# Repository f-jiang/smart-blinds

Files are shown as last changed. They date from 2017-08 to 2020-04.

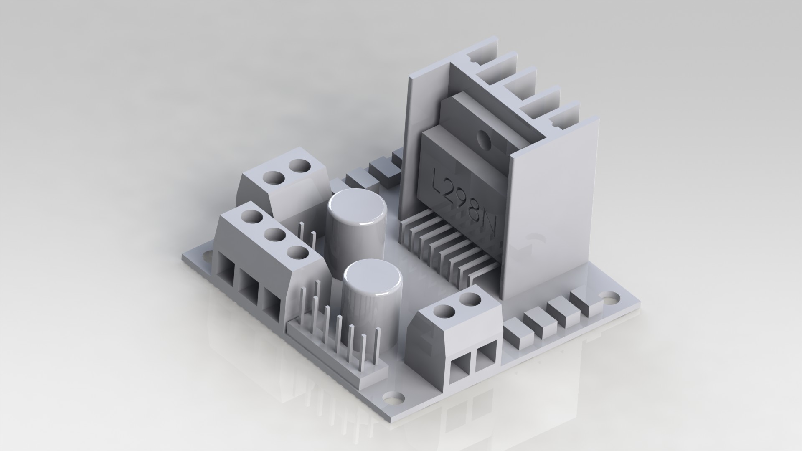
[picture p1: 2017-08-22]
cad/parts/arduino-l298n-1.snapshot.1/FOTO.JPG

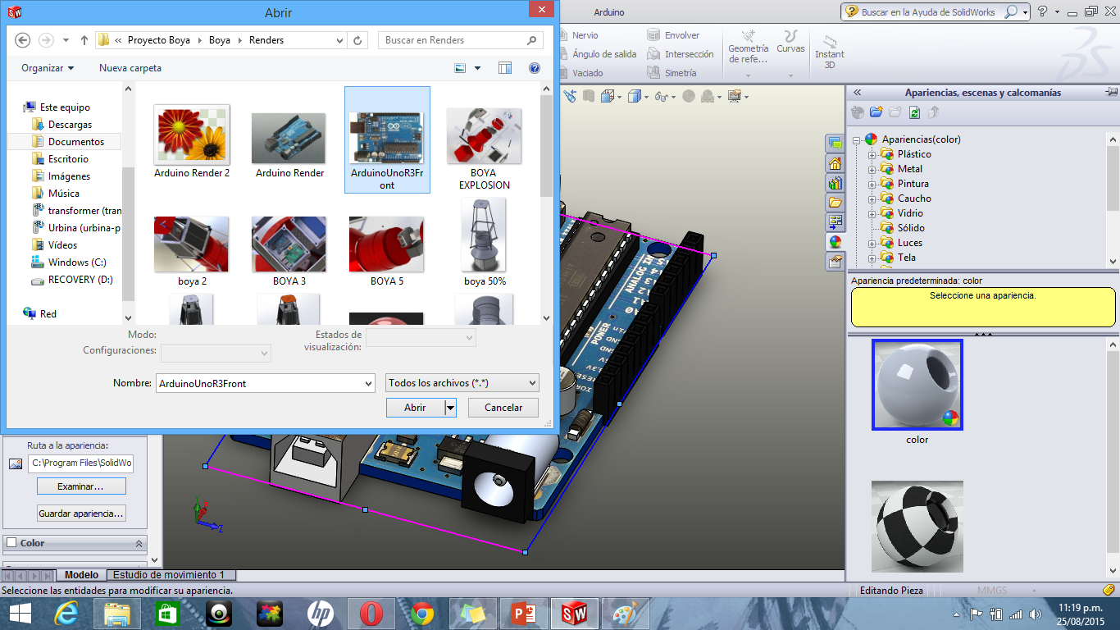
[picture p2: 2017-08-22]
cad/parts/arduino-uno-4.snapshot.3/Renderings/Add Backgroud 2.png

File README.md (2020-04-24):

# smart-blinds
Smart-home blinds attachment with remote-control and scheduling capabilities. Device consists of a stepper motor with an attachment for turning blinds cords and is controlled by an Arduino Uno board. An ESP8266 enables the device to communicate on the network using MQTT. Home Assistant is used for scheduling and remote-control capabilities. The blinds can also be controlled manually using two buttons.

# Repo Contents

## `arduino-src`

Source code for the blinds attachment

```
arduino-src/
├── mqtt_client  # code for ESP8266, used to grant the Arduino board network access thru the MQTT protocol
│   └── mqtt_client.ino
└── smart_blinds  # arduino code for physical control of the blinds attachment
    ├── smart_blinds.h
    ├── smart_blinds.ino  # arduino sketch
    ├── tests.cpp  # "unit tests"
    ├── tests.h
    └── wear_leveled_eeprom_object.h  # utility for storing motor position, etc. in EEPROM in a wear-minimizing way
```

## `cad`

CAD drawings and assemblies. CAD packages used: AutoCAD 2016, SOLIDWORKS 2017

```
cad/
├── exports
│   └── baseplate.DWG  # chassis drawing, to be laser-cut on acrylic
├── parts  # SOLIDWORKS parts
│   ├── arduino-l298n-1.snapshot.1
│   ├── arduino-uno-4.snapshot.3
│   ├── baseplate.SLDPRT  # acrylic chassis
│   ├── cord gear  # 3d-printed blinds cord attachment
│   ├── motherboard-stand-standoff-screw-1.snapshot.1
│   ├── nema-17-nema-23-stepper-motor-mounts-1.snapshot.4
│   ├── nema-17-stepper-motor-13.snapshot.1
│   └── protoboard-5x7-cm.SLDPRT  # perfboard containing mostly power circuitry
└── smart-blinds.SLDASM  # SOLIDWORKS assembly
```

## `docs`

Misc. notes, including technical details, logged work, and unused ideas

## `home-assistant-config`

Setup files for Home Assistant home automation platform

```
home-assistant-config/
├── automations.yaml  # config code to make blinds open/close at sunrise/sunset
├── configuration.yaml  # basic setup including MQTT topic definitions
├── customize.yaml
├── groups.yaml
├── scripts.yaml
└── secrets.yaml
```

# Retrospective
- Could have used ESP32, which has both WiFi capability and enough pins for motor control etc.
- Linear regulators are too hot and inefficient for large voltage stepdowns
- Stepper motors are too big and heavy and lack position control on their own. Could have used a high-torque servo instead.

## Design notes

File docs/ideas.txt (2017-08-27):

mechanical design:
- make the stepper motor's position adjustable
  - attach the motor to a flexible tube-like arm
- reduce blinds cord slippage
  - by using a vertical holder
  - by cutting out a "circle" of holes, allowing the l-bracket to be mounted at a variey of angles

mobile app:
- automatically determine opening and closing times based on location

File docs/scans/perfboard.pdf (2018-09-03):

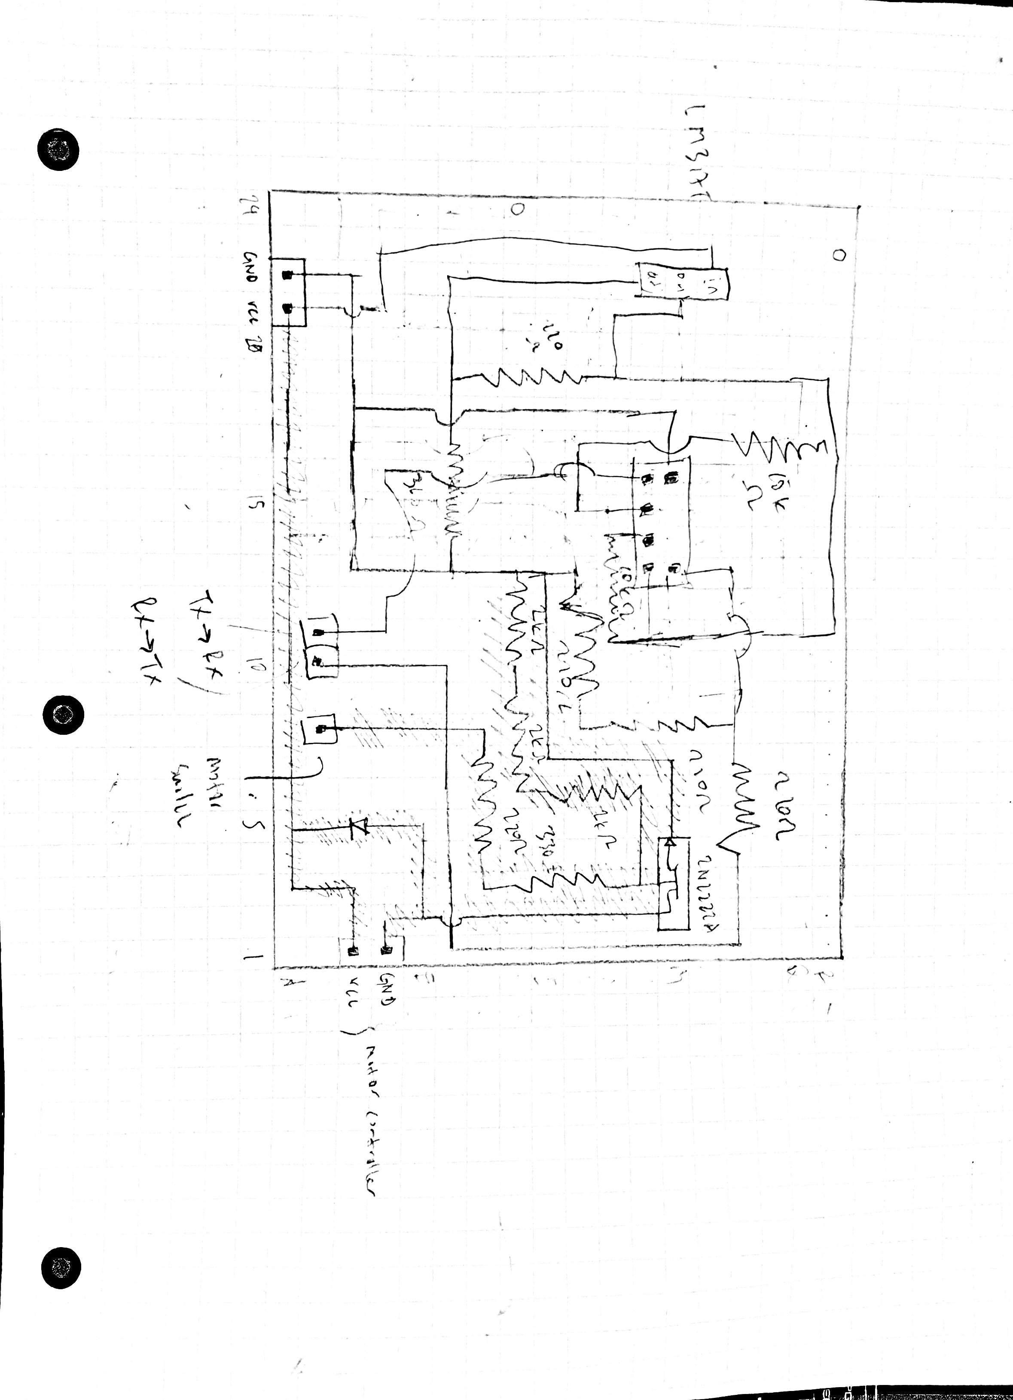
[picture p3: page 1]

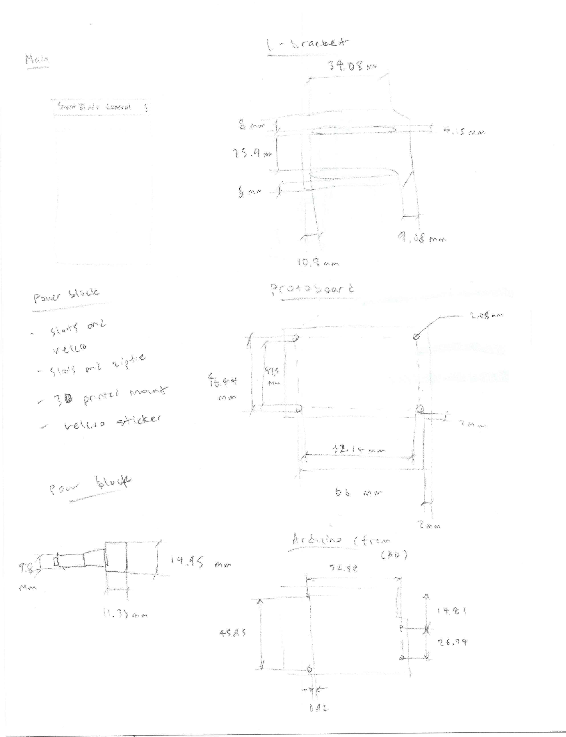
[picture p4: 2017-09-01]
docs/scans/dimensions.jpg

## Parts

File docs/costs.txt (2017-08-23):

- arduino uno: ~$15
- [sensor shield]: $13
- bluetooth module: $10
- motor controller: $14
- motor: $19
- motor bracket: $10
- 12V adapter: $14
- protoboard: $0.30

- acrylic board
- screws, standoffs, etc.
- motor attachments

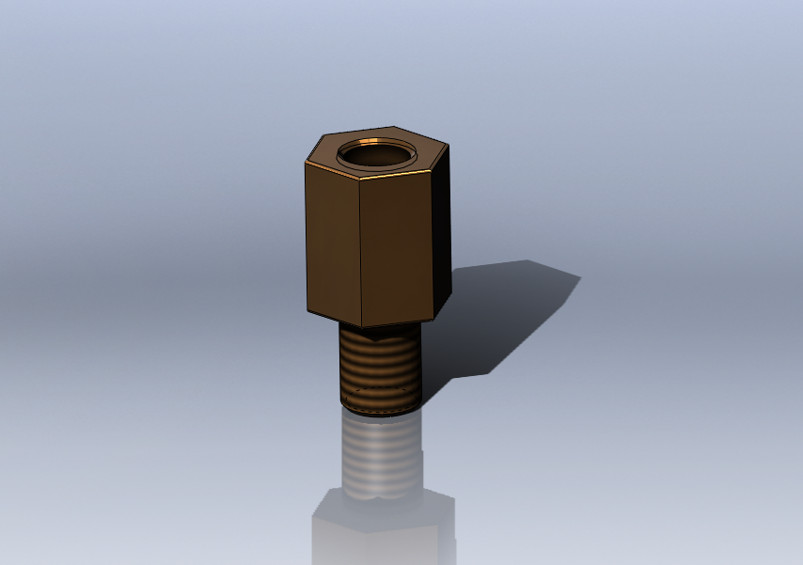
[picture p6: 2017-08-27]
cad/parts/motherboard-stand-standoff-screw-1.snapshot.1/m_standoff.PNG

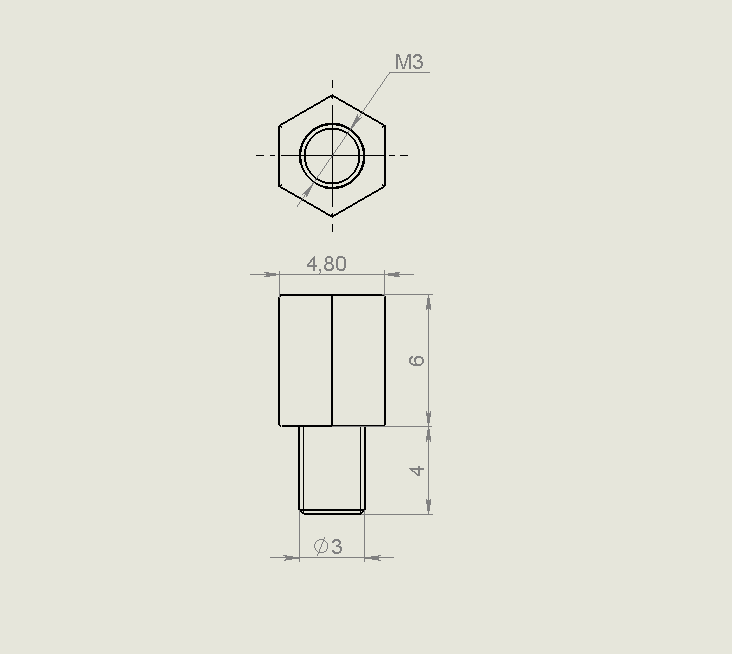
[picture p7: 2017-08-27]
cad/parts/motherboard-stand-standoff-screw-1.snapshot.1/m_standoff_size.PNG

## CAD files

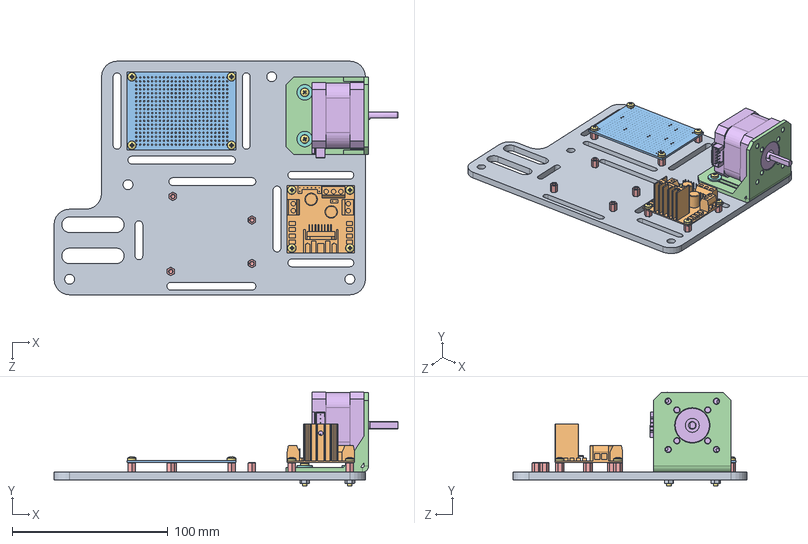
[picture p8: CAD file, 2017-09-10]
cad/smart-blinds.SLDASM
220.9 x 60.0 x 150.0 mm
baseplate
L298N
protoboard-5x7-cm
MotorMount_NEMA
motherboard_stand x 12
Nema 17 motor
pan cross head_am x 12
flat washer regular_am x 4
hex nut style 1_am x 4

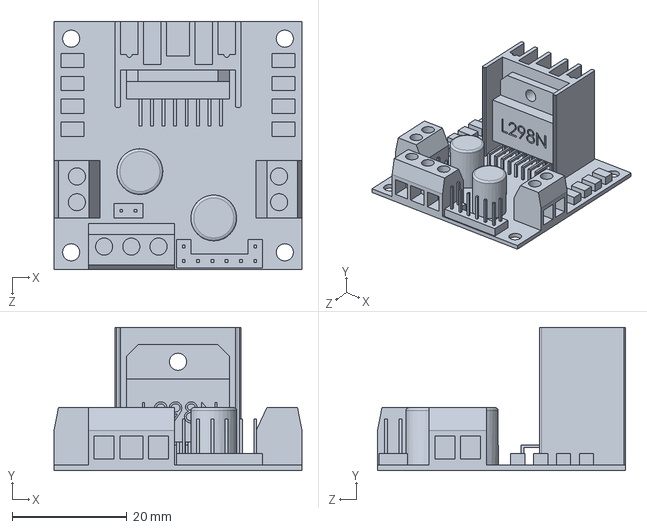
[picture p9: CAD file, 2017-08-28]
cad/parts/arduino-l298n-1.snapshot.1/L298N.SLDPRT
43.3 x 25.0 x 43.3 mm

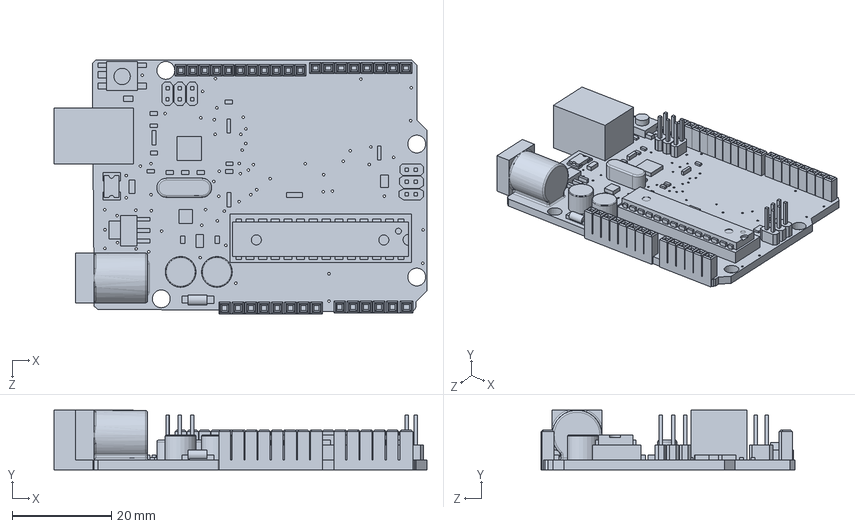
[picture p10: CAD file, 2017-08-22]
cad/parts/arduino-uno-4.snapshot.3/Arduino.SLDPRT
75.0 x 12.0 x 51.0 mm

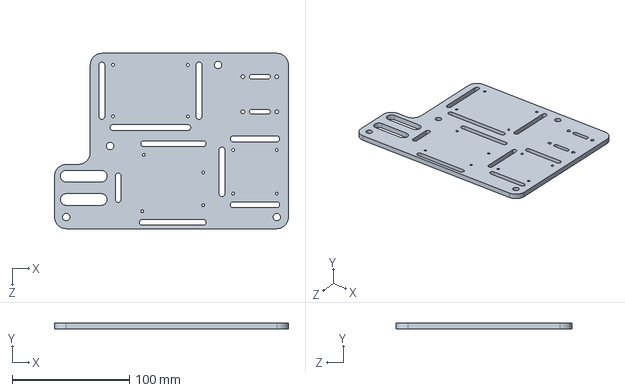
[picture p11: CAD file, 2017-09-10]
cad/parts/baseplate.SLDPRT
200.0 x 5.00 x 150.0 mm

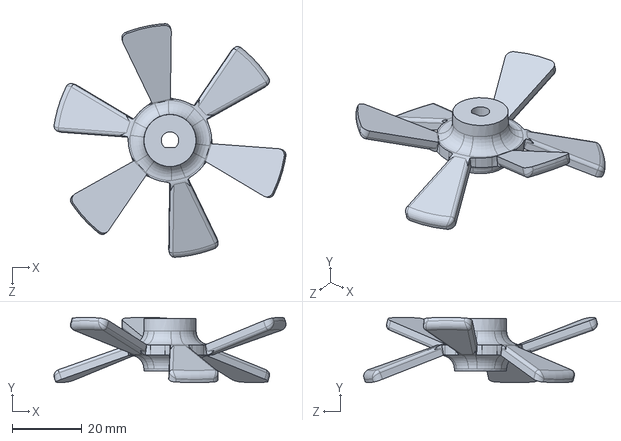
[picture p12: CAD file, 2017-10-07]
cad/parts/cord gear/cord gear.SLDPRT
66.7 x 18.7 x 67.1 mm

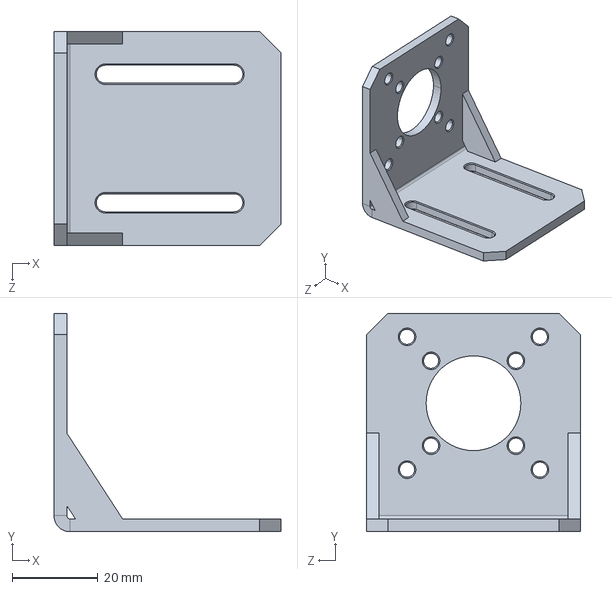
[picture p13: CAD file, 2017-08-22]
cad/parts/nema-17-nema-23-stepper-motor-mounts-1.snapshot.4/NEMA17MotorMount.STEP
53.0 x 51.0 x 50.0 mm

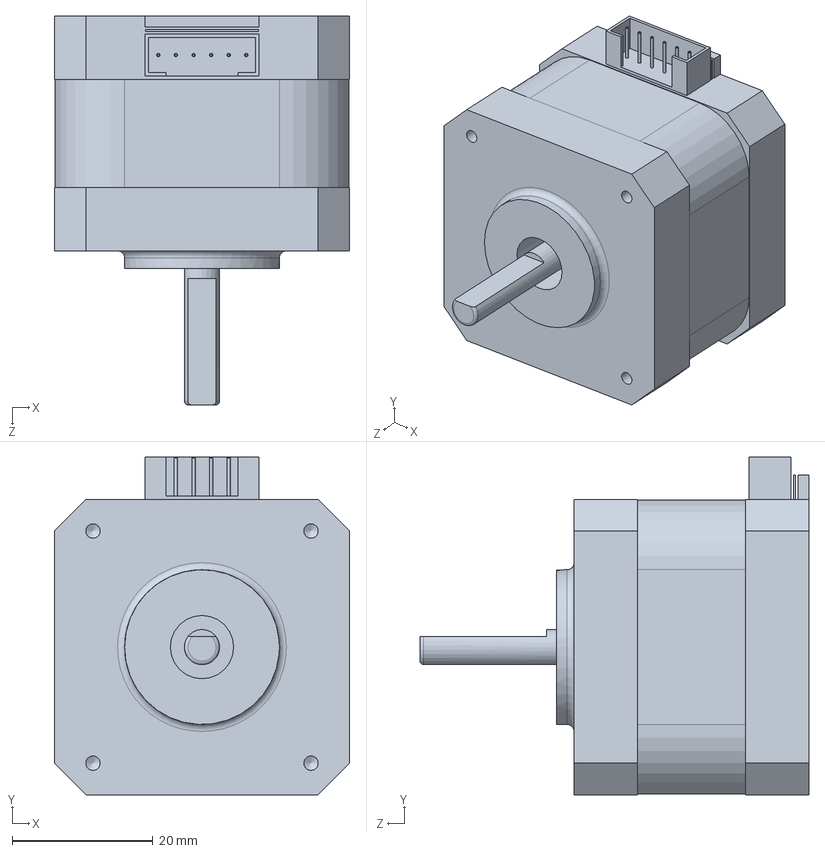
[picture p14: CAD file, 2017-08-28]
cad/parts/nema-17-stepper-motor-13.snapshot.1/Nema 17 motor.SLDPRT
42.0 x 48.0 x 55.3 mm

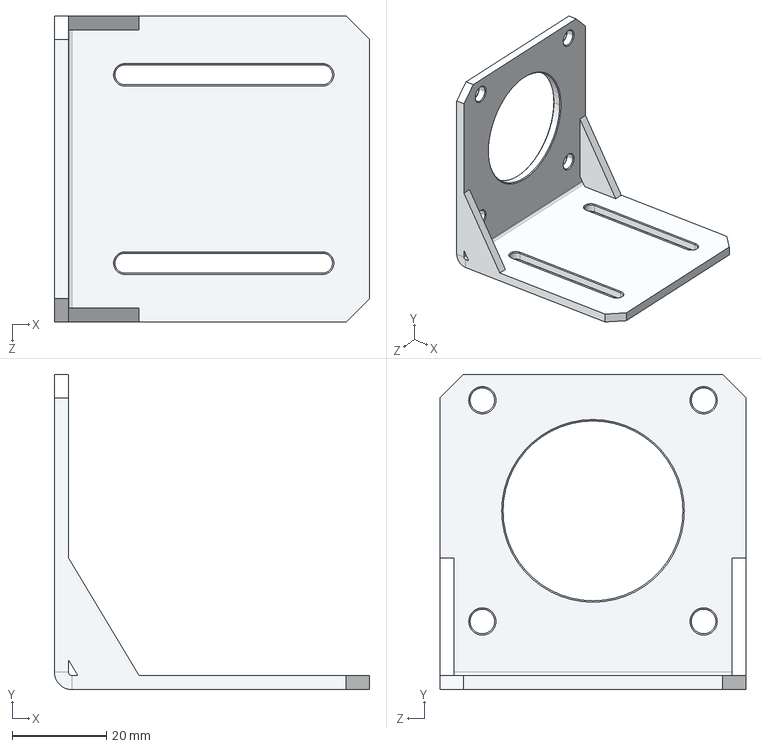
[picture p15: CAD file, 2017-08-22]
cad/parts/nema-17-nema-23-stepper-motor-mounts-1.snapshot.4/NEMA23MotorMount.STEP
67.0 x 67.0 x 65.0 mm

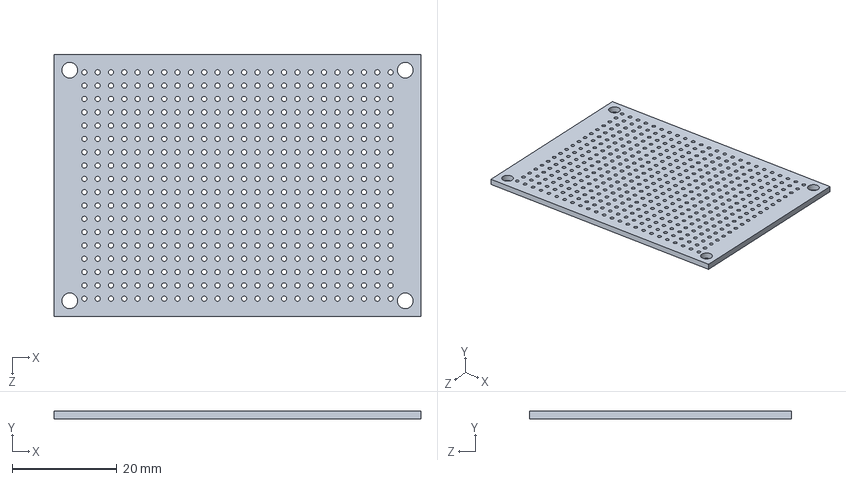
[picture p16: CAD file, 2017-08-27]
cad/parts/protoboard-5x7-cm.SLDPRT
70.0 x 1.50 x 50.0 mm

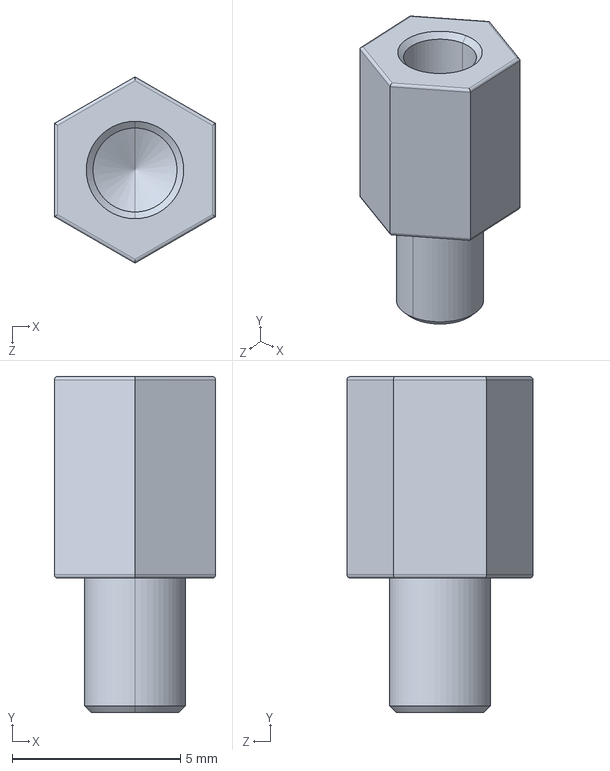
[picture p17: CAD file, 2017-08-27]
cad/parts/motherboard-stand-standoff-screw-1.snapshot.1/motherboard_stand.STP
4.80 x 10.0 x 5.54 mm

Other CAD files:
cad/parts/nema-17-nema-23-stepper-motor-mounts-1.snapshot.4/MotorMount_NEMA.SLDPRT
cad/exports/baseplate.DWG
cad/parts/cord gear/cord gear.STL
cad/parts/motherboard-stand-standoff-screw-1.snapshot.1/motherboard_stand.SLDPRT
cad/parts/nema-17-nema-23-stepper-motor-mounts-1.snapshot.4/NEMA17MotorMount.STL
cad/parts/nema-17-nema-23-stepper-motor-mounts-1.snapshot.4/NEMA23MotorMount.STL

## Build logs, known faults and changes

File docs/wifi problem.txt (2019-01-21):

- tried setting up esp8266 according to several tutorials; each one gave me the same result, which is no response from esp8266
  - http://www.teomaragakis.com/hardware/electronics/how-to-connect-an-esp8266-to-an-arduino-uno/
  - https://www.deviceplus.com/how-tos/arduino-guide/esp8266-setup-tutorial-using-arduino/
 
- also tried talking to esp8266 directly via serial (uploaded blank sketch to arduino): get some junk data but no response of any sort

- tried flashing firmware according to following tutorial:
  - https://www.electronicshub.org/update-flash-esp8266-firmware/
    - result: status FAIL or ERROR; also the DETECTED INFO section is blank and before failure the status is stuck at SYNC, even though serial port is detected
    
1/13/19:
  - plugged new esp into perboard circuit; used 115200 baud, and was getting response from esp but garbled
    - also the blue led was staying on for longer and longer each time
  - then built deviceplus circuit on breadboard, got clear responses from esp at 9600 baud
  - put same esp back into perfboard circuit but now using 9600 baud; now esp blue led always on and no longer getting responses
    - this is how the second esp broke
    - when reset esp will still output firmware info, same as second "broken" esp
- ideas for what happened
  - there is something wrong with my perfboard circuit: either incorrect schematics (didn't follow device plus circuit accurately) or poor layout of components, resulting in esp getting damaged
  - the device plus circuit is flawed
  - maybe esp is fixable
  
1/19/19:
- with ftdi converter, boot message at 74880 baud, but no response from AT commands regardless of baud
- another reason not working:
  - maybe board is just bricked not broken -> try reflashing firmware using esptool.py according to this guide: https://bbs.espressif.com/viewtopic.php?t=4597#p15844
    - step 1: set up python esptool:
      - erase flash - done
    - step 2: get and flash firmware
    - worked
    - commands to enter for reflashing for 8Mb flash:
      esptool.py erase_flash
      esptool.py --port <port> write_flash -fm qio 0x00000 boot_v1.7.bin
      esptool.py --port <port> write_flash -fm qio 0x01000 user1.1024.new.2.bin
      esptool.py --port <port> write_flash -fm qio 0xfc000 esp_init_data_default.bin
      esptool.py --port <port> write_flash -fm qio 0x7e000 blank.bin
- so true cause: AT+IPR=9600 bricks the board
  - instead use AT+UART_DEF to change the baud rate
  - For example 9600 baudrate / 8 data bits / 1 stop bits and none parity and flow control
    AT+UART_DEF=9600,8,1,0,0

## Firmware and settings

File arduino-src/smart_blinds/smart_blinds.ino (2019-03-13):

/* #define TEST */
#define DEBUG

#include "smart_blinds.h"

#include <stdlib.h>
#include <SoftwareSerial.h>
#ifdef TEST
#include "tests.h"
#endif
#include "wear_leveled_eeprom_object.h"

#define SERIAL_BAUD_RATE            9600
#define SOFTWARE_SERIAL_BAUD_RATE   9600

#define STEPPER_A                   2
#define STEPPER_B                   3
#define STEPPER_C                   4
#define STEPPER_D                   5
#define RPM                         15
#define STEP_ANGLE                  1.8
#define STEPS_PER_REVOLUTION        (360.0 / STEP_ANGLE)

#define RELAY_PIN                   6

#define BUTTON_PIN                  7

#define ESP_RX                      8
#define ESP_TX                      9

#define COMMAND_TILT                't'
#define COMMAND_CALIBRATE_HIGH      'h'
#define COMMAND_CALIBRATE_LOW       'l'

#define STR_BUF_LEN                 10

Stepper stepper(STEPS_PER_REVOLUTION, STEPPER_A, STEPPER_B, STEPPER_C, STEPPER_D);
Relay relay(RELAY_PIN, Relay::Mode::NORMALLY_OPEN);
ace_button::AceButton btn(BUTTON_PIN);
SoftwareSerial esp(ESP_RX, ESP_TX);

size_t circularQueueItemCount = EEPROM_SIZE_BYTES /
                                (3 * WearLeveledEepromObject<stepper_pos_t>::circularQueueItemSize());
WearLeveledEepromObject<stepper_pos_t> stepperPos(0, circularQueueItemCount);
WearLeveledEepromObject<stepper_pos_t> stepperPosLowerLimit(EEPROM_SIZE_BYTES / 3, circularQueueItemCount);
WearLeveledEepromObject<stepper_pos_t> stepperPosUpperLimit(2 * EEPROM_SIZE_BYTES / 3, circularQueueItemCount);
stepper_pos_t eepromValue;

void setup()
{
    Serial.begin(SERIAL_BAUD_RATE);

    if (stepperPos.get(eepromValue) == 0xFFFF &&
        stepperPosLowerLimit.get(eepromValue) == 0xFFFF &&
        stepperPosUpperLimit.get(eepromValue) == 0xFFFF)
    {
#ifdef DEBUG
        Serial.println("no position or limits in storage; using defaults instead");
#endif
        eepromValue = STEPPER_POSITION_DEFAULT;
        stepperPos.put(eepromValue);
        eepromValue = STEPPER_POSITION_LOWER_LIMIT_DEFAULT;
        stepperPosLowerLimit.put(eepromValue);
        eepromValue = STEPPER_POSITION_UPPER_LIMIT_DEFAULT;
        stepperPosUpperLimit.put(eepromValue);
#ifndef DEBUG
    }
#else
    } else {
        stepper_pos_t pos, lower_limit, upper_limit;
        stepperPos.get(pos);
        stepperPosLowerLimit.get(lower_limit);
        stepperPosUpperLimit.get(upper_limit);

        Serial.print("found following in storage: position ");
        Serial.print(pos);
        Serial.print(", lower limit ");
        Serial.print(lower_limit);
        Serial.print(", upper limit ");
        Serial.println(upper_limit);
    }
#endif

    relay.begin();
    stepper.setSpeed(RPM);
#ifdef DEBUG
    Serial.print("stepper speed set to ");
    Serial.print(RPM);
    Serial.println(" rpm");
#endif

    pinMode(BUTTON_PIN, INPUT_PULLUP);
    btn.setEventHandler(handleBtnEvent);

    relay.open();

    esp.begin(SOFTWARE_SERIAL_BAUD_RATE);

#ifdef TEST
    Serial.println("Running tests...");
    test();
    Serial.println("Tests complete and successful");
#endif
}

void loop()
{
#ifndef TEST
    btn.check();

    if (esp.available() > 0) {
        String data;
        while (esp.available() > 0) {
            data += (char) esp.read();
        }

#ifdef DEBUG
        Serial.print("received data from serial: ");
        Serial.println(data);
#endif

        char command = data.charAt(0);
        data.remove(0, 1);
        int value = data.toInt();
        stepper_pos_t new_value;
        char buf[STR_BUF_LEN];

#ifdef DEBUG
        Serial.print("values extracted from incoming serial data: command ");
        Serial.print(command);
        Serial.print(", value ");
        Serial.println(value);
#endif

        switch (command) {
            case COMMAND_TILT:
                if (data.length() > 0) {
                    setStepperPos((stepper_pos_t) value);
                }

                getStepperPos(new_value);
                sprintf(buf, "%c%d", COMMAND_TILT, new_value);
                esp.write(buf);

#ifdef DEBUG
                Serial.print("new stepper position: ");
                Serial.println(new_value);
#endif
                break;
            case COMMAND_CALIBRATE_HIGH:
                if (data.length() > 0) {
                    relay.open();
                    setStepperPosUpperLimit((stepper_pos_t) value);
                }

                getStepperPosUpperLimit(new_value);
                sprintf(buf, "%c%d", COMMAND_CALIBRATE_HIGH, new_value);
                esp.write(buf);

#ifdef DEBUG
                Serial.print("new stepper upper limit: ");
                Serial.println(new_value);
#endif
                break;
            case COMMAND_CALIBRATE_LOW:
                if (data.length() > 0) {
                    relay.open();
                    setStepperPosLowerLimit((stepper_pos_t) value);
                }

                getStepperPosLowerLimit(new_value);
                sprintf(buf, "%c%d", COMMAND_CALIBRATE_LOW, new_value);
                esp.write(buf);

#ifdef DEBUG
                Serial.print("new stepper lower limit: ");
                Serial.println(new_value);
#endif
                break;
            default:
#ifdef DEBUG
                Serial.println("not a valid command");
#endif
                break;
        }
    }

    delay(100);
#endif
}

void handleBtnEvent(ace_button::AceButton* /*button*/, uint8_t eventType, uint8_t /*state*/)
{
    switch (eventType) {
        case ace_button::AceButton::kEventReleased:
        {
#ifdef DEBUG
            Serial.println("button press detected");
#endif

            stepper_pos_t pos, lowerLimit;
            stepperPos.get(pos);
            stepperPos.get(lowerLimit);

            setStepperPos((pos == lowerLimit) ?
                          stepperPosUpperLimit.get(eepromValue) : stepperPosLowerLimit.get(eepromValue));

            stepper_pos_t new_value;
            char buf[STR_BUF_LEN];
            getStepperPos(new_value);
            sprintf(buf, "%d", new_value);
            esp.write(COMMAND_TILT);
            esp.write(buf);

#ifdef DEBUG
            Serial.print("new stepper position: ");
            Serial.print(new_value);
            Serial.print(" (");
            Serial.print((new_value == lowerLimit) ? "lower" : "upper");
            Serial.println(" limit)");
#endif
            break;
        }
        default:
            break;
    }
}

bool isPosInverted()
{
    return stepperPosUpperLimit.get(eepromValue) < stepperPosLowerLimit.get(eepromValue);
}

bool isStepperCalibrated()
{
    return (stepperPos.get(eepromValue) != STEPPER_POSITION_DEFAULT) &&
           (stepperPosLowerLimit.get(eepromValue) != STEPPER_POSITION_LOWER_LIMIT_DEFAULT) &&
           (stepperPosUpperLimit.get(eepromValue) != STEPPER_POSITION_UPPER_LIMIT_DEFAULT);
}

bool isPosOutOfBounds(stepper_pos_t pos)
{
    bool retval;

    bool inverted = isPosInverted();
    if ((!inverted &&
         (stepperPosLowerLimit.get(eepromValue) <= pos) &&
         (pos <= stepperPosUpperLimit.get(eepromValue))) ||
        (inverted &&
         (stepperPosUpperLimit.get(eepromValue) <= pos) &&
         (pos <= stepperPosLowerLimit.get(eepromValue)))) {
        retval = false;
    } else {
        retval = true;
    }

    return retval;
}

bool getStepperPos(stepper_pos_t& pos)
{
    bool success = false;

    if (true) { // TODO temp
        success = true;
        stepperPos.get(pos);
    }

    return success;
}

bool setStepperPos(stepper_pos_t pos)
{
    bool success = false;

    if (!isPosOutOfBounds(pos)) {
        success = true;

        stepper_pos_t stepValue;

        if (isPosInverted()) {
            stepValue = stepperPos.get(eepromValue) - pos;
        } else {
            stepValue = pos - stepperPos.get(eepromValue);
        } /* else {
            success = false;
        } */

        if (success && stepValue != 0) {
            relay.close();
            stepper.step(stepValue);
            relay.open();
            stepperPos.put(pos);
        }
#ifndef DEBUG
    }
#else
        Serial.print("set stepper position to ");
        Serial.println(pos);
    } else if (!relay.isClosed()) {
        Serial.println("setting stepper position failed because relay is open");
    } else {
        Serial.println("setting stepper position failed because new position is out-of-bounds");
    }
#endif

    return success;
}

bool getStepperPosLowerLimit(stepper_pos_t& pos)
{
    bool success = false;

    if (true) { // TODO temp
        success = true;
        stepperPosLowerLimit.get(pos);
    }

    return success;
}

// TODO enforce lower != upper?
bool setStepperPosLowerLimit(stepper_pos_t pos)
{
    bool success = false;

    if (!relay.isClosed()) {
        success = true;
        stepperPosLowerLimit.put(pos);
    }

    return success;
}

bool getStepperPosUpperLimit(stepper_pos_t& pos)
{
    bool success = false;

    if (true) { // TODO temp
        success = true;
        stepperPosUpperLimit.get(pos);
    }

    return success;
}

// TODO enforce lower != upper?
bool setStepperPosUpperLimit(stepper_pos_t pos)
{
    bool success = false;

    if (!relay.isClosed()) {
        success = true;
        stepperPosUpperLimit.put(pos);
    }

    return success;
}

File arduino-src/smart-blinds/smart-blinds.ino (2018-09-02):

#define TEST_DEBUG

#include "smart-blinds.h"

#ifdef TEST_DEBUG
#include "tests.h"
#endif  // TEST_DEBUG

#define STEPPER_A               8
#define STEPPER_B               9
#define STEPPER_C               10
#define STEPPER_D               11
#define RPM                     15
#define STEP_ANGLE              1.8
#define STEPS_PER_REVOLUTION    (360.0 / STEP_ANGLE)

#define RELAY_PIN               6

#define BUTTON_PIN              7

Stepper stepper(STEPS_PER_REVOLUTION, STEPPER_A, STEPPER_B, STEPPER_C, STEPPER_D);
Relay relay(RELAY_PIN, Relay::Mode::NORMALLY_OPEN);
int stepperPos = STEPPER_POSITION_DEFAULT;
int stepperPosLowerLimit = STEPPER_POSITION_LOWER_LIMIT_DEFAULT;
int stepperPosUpperLimit = STEPPER_POSITION_UPPER_LIMIT_DEFAULT;

void setup()
{
    Serial.begin(9600);

    // TODO load position from eeprom

    relay.begin();
    stepper.setSpeed(RPM);

    relay.open();

#ifdef TEST_DEBUG
    Serial.println("Running tests...");
    test();
    Serial.println("Tests complete and successful");
#endif  // TEST_DEBUG
}

void loop()
{
}

StepperPositionScaleType getStepperPositionScaleType()
{
    StepperPositionScaleType retval;

    if (stepperPosLowerLimit <= stepperPosUpperLimit) {
        retval = NORMAL;
    } else {
        retval = INVERTED;
    }

    return retval;
}

bool isStepperCalibrated()
{
    return (stepperPos != STEPPER_POSITION_DEFAULT) &&
           (stepperPosLowerLimit != STEPPER_POSITION_LOWER_LIMIT_DEFAULT) &&
           (stepperPosUpperLimit != STEPPER_POSITION_UPPER_LIMIT_DEFAULT);
}

bool isPosOutOfBounds(int pos)
{
    bool retval;

    StepperPositionScaleType scaleType = getStepperPositionScaleType();
    if (((scaleType == NORMAL) &&
         (stepperPosLowerLimit <= pos) &&
         (pos <= stepperPosUpperLimit)) ||
        ((scaleType == INVERTED) &&
         (stepperPosUpperLimit <= pos) &&
         (pos <= stepperPosLowerLimit))) {
        retval = false;
    } else {
        retval = true;
    }

    return retval;
}

bool getStepperPos(int& pos)
{
    bool success = false;

    if (true) { // TODO temp
        success = true;
        pos = stepperPos;
    }

    return success;
}

bool setStepperPos(int pos)
{
    bool success = false;

    if (relay.isClosed() && !isPosOutOfBounds(pos)) {
        success = true;

        int stepValue;
        StepperPositionScaleType scaleType = getStepperPositionScaleType();

        if (scaleType == NORMAL) {
            stepValue = pos - stepperPos;
        } else if (scaleType == INVERTED) {
            stepValue = stepperPos - pos;
        } else {
            success = false;
        }

        if (success) {
            stepper.step(stepValue);
            stepperPos = pos;
        }
    }

    return success;
}

bool incrementStepperPos()
{
    bool success = true;

    int newPos;
    StepperPositionScaleType scaleType = getStepperPositionScaleType();

    if (scaleType == NORMAL) {
        newPos = stepperPos + STEP_INCREMENT_SIZE;
    } else if (scaleType == INVERTED) {
        newPos = stepperPos - STEP_INCREMENT_SIZE;
    }

    if (success) {
        success = setStepperPos(newPos);
    }

    return success;
}

bool decrementStepperPos()
{
    bool success = true;

    int newPos;
    StepperPositionScaleType scaleType = getStepperPositionScaleType();

    if (scaleType == NORMAL) {
        newPos = stepperPos - STEP_INCREMENT_SIZE;
    } else if (scaleType == INVERTED) {
        newPos = stepperPos + STEP_INCREMENT_SIZE;
    }

    if (success) {
        success = setStepperPos(newPos);
    }

    return success;
}

bool getStepperPosLowerLimit(int& pos)
{
    bool success = false;

    if (true) { // TODO temp
        success = true;
        pos = stepperPosLowerLimit;
    }

    return success;
}

// TODO enforce lower != upper?
bool setStepperPosLowerLimit(int pos)
{
    bool success = false;

    if (!relay.isClosed()) {
        success = true;
        stepperPosLowerLimit = pos;
    }

    return success;
}

bool getStepperPosUpperLimit(int& pos)
{
    bool success = false;

    if (true) { // TODO temp
        success = true;
        pos = stepperPosUpperLimit;
    }

    return success;
}

// TODO enforce lower != upper?
bool setStepperPosUpperLimit(int pos)
{
    bool success = false;

    if (!relay.isClosed()) {
        success = true;
        stepperPosUpperLimit = pos;
    }

    return success;
}

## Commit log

2017-08-22 Initial commit
    current contents:
    - cad files for each part
    - dimensions
    - list of parts and their costs
    [10 PORT HEADER.SLDPRT, 2pin_header__02.sldprt, 47uf CAP.SLDPRT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]
2017-08-22 tentative wiring schematic
2017-08-22 list fasteners needed for mounting
2017-08-22 reorganize cad files
    [10 PORT HEADER.SLDPRT, 2pin_header__02.sldprt, 47uf CAP.SLDPRT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]
2017-08-22 add relay board model
    [SAINSMART 8 CHANNEL DC 5V RELAY MODULE.IGS, SAINSMART 8 CHANNEL DC 5V RELAY MODULE.SLDPRT, SAINSMART 8 CHANNEL DC 5V RELAY MODULE.STEP]
2017-08-22 create tentative baseboard layout
    [baseplate.SLDPRT]
2017-08-23 wiring update
2017-08-23 replace relay with transistor switch
    - protoboard hole spacing is tentative
    [baseplate.SLDPRT]
2017-08-27 cad: final dimensions for all holes and slots
    [baseplate.SLDPRT]
2017-08-27 cad: position baseboard-mounted components
    [baseplate.SLDPRT]
2017-08-27 organize files
    [baseplate.SLDPRT]
2017-08-27 cad: create protoboard model
    [protoboard-5x7-cm.SLDPRT]
2017-08-27 cad: remove unneeded files
    [10 PORT HEADER.SLDPRT, 2pin_header__02.sldprt, 47uf CAP.SLDPRT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]
2017-08-27 cad: correct some baseplate holes components affected: - l298n - protoboard
    [baseplate.SLDPRT]
2017-08-27 cad: add standoff screw model
    [motherboard_stand.SLDPRT, motherboard_stand.STP]
2017-08-28 cad: add smart blinds assembly (wip)
    [L298N.SLDPRT, Nema 17 motor.SLDPRT, motherboard_stand.SLDPRT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]
2017-08-29 cad: add cable management slots to baseplate
    [baseplate.SLDPRT]
2017-08-29 cad: material reduction and mounting holes
    [baseplate.SLDPRT]
2017-08-29 cad: add .dwg file of baseplate for cutting
    [baseplate.DWG]
2017-09-01 docs: add scans
    - dimensioned drawings of mounted boards
    - rough diagram of wires that may have to pass over/under boards other than those that they connect to
2017-09-10 cad: update baseplate
    - relocate l-bracket cable management slots so that they are in between the mounting holes
    - increase spacing between slots and mounting holes
    [baseplate.DWG, baseplate.SLDPRT, smart-blinds.SLDASM]
2017-09-30 app: add switches to main preferences
2017-09-30 app: add default values for main screen switches
2017-10-06 cad: add basic design for cord gear
    [cord gear.SLDPRT]
2017-10-07 cad: adjust cord gear dims
    [cord gear.SLDPRT]
2017-10-07 cad: export stl of cord gear
    [cord gear.SLDPRT, cord gear.STL]
2017-10-07 cad: add cord gear fillets and secure shaft connection
    [cord gear.SLDPRT, cord gear.STL]
2017-10-09 app: add blinds calibration activity
2018-07-02 update wiring diagram after wifi module addition
2018-07-02 update wiring diagram to get rid of overlap
2018-07-02 revise transistor switching circuit
2018-07-30 fix and update wiring diagram
    - esp CP_PD and RESET go to 3.3 V high
    - legend update
2018-08-28 replace transistor switch with relay
2018-08-30 add pushbutton to wiring
2018-09-01 add stepper code and tests
2018-09-02 fix error with comparing wrong pos value
    [smart-blinds.ino]
2018-09-02 lower motor speed
2018-09-02 fix test out-of-bounds test position
    [smart-blinds.ino]
2018-09-02 set new position by moving motor for tests
2018-09-02 increase stepper movements for tests
2018-09-02 print test status
2018-09-02 arduino-src: function indentation
2018-09-02 arduino-src: separate tests into own file
2018-09-02 arduino-src: turn off stepper on startup
2018-09-02 arduino-src: rename position macros and redefine undefined pos value
2018-09-02 change uncalibrated definition and behaviour
    - remove undefined position and scale type
    - uncalibrated now means that there are no limits on position, not that position
    is undefined
    - can now move stepper motor and get position when uncalibrated
2018-09-03 docs: fix relay control wire type
2018-09-04 arduino-src: remap stepper pins
2018-09-04 arduino-src: implement eeprom wear-levelling for position and limits storage
2018-09-15 arduino-src: fix eeprom get and put
2018-09-15 arduino-src: disable eeprom default ctor
2018-09-15 arduino-src: add eeprom tests
2018-09-15 arduino-src: make case consistent
2018-10-07 fix and update eeprom tests
    - use queue item size instead of data type size for queue size tests
    - fix incorrect check for queue end address
    - store a different value each time for eeprom tests
    [tests.cpp]
2018-10-07 fix eeprom errors
    - update current address and current object each time new value written
    - define a constant for unused position of value UINT16_MAX
    - update arg reference after value read from eeprom
    - initialize first eeprom object to 0
2018-10-30 arduino-src: program btn for toggling position
2019-01-27 arduino-src: add esp connect and request for response from app
2019-02-17 arduino-src: remove esp at commands interfacing
2019-02-17 arduino-src: remove unneeded position inversion enum
2019-02-18 arduino-src: add esp mqtt client
2019-02-18 arduino-src: remove stepper (in|de)crement fns
2019-02-20 arduino-src: use stepper_pos_t for position values
2019-02-20 arduino-src: always use same value for eeprom storage test
2019-02-20 arduino-src: implement saving position to eeprom
2019-02-20 arduino-src: baud rate consts for smart_blinds
2019-02-20 arduino-src: implement comms receiver on smart blinds
2019-02-20 arduino-src: add smart blinds debug statements
2019-02-20 arduino-src: change eeprom blank value to 1
2019-02-20 arduino-src: fix upper limit debugger statement
    [smart_blinds.ino]
2019-02-20 arduino-src: write position after stepper pos update
2019-02-21 arduino-src: fix debug print for mqtt client
    [mqtt_client.ino]
2019-03-12 arduino-src: fix arduino-to-esp serial comms
    add delay between incoming data reads on esp so that enough time for buffer to get sent to esp
    [mqtt_client.ino]
2019-03-12 arduino-src: store all serial msg data in one buf
2019-03-12 arduino-src: only toggle relay if motor really will be set
2019-03-13 arduino-src: add ability to get tilt positions and limits via mqtt
2019-05-15 cad: reorganize exported files
    [baseplate.DWG]
